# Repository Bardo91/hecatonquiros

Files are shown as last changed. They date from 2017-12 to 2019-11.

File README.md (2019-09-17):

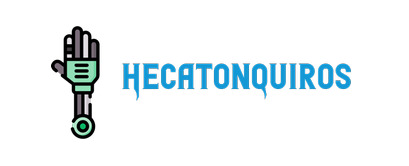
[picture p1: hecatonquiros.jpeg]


    

[WIKI](https://github.com/ViGUS/hecatonquiros/wiki)

Official doc in https://vigus.github.io/hecatonquiros/

# INSTALLATION

1. Install dependencies
```
git clone https://github.com/Bardo91/hecatonquiros
cd hecatonquiros
bash scripts/install_dependencies.sh
```
2. Compile library and install
```
cd build
cmake ..
make -j4
sudo make install
```

# TUTORIALS
[tutorial gazebo](https://github.com/ViGUS/hecatonquiros/wiki/Tutorial-gazebo)

# Arm models
###  PWM servos Model 4 DoF

###  Feetech serial servos Model 4 DoF
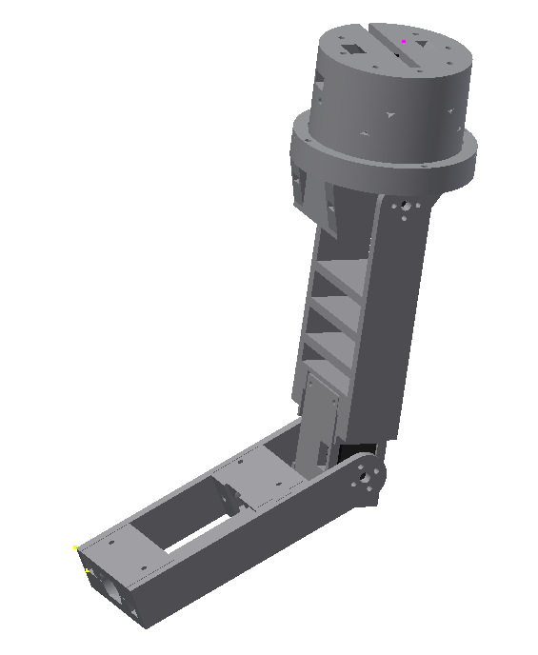
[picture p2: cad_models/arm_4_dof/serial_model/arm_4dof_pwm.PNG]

# Tools
### Gripper 0 Dof PWM
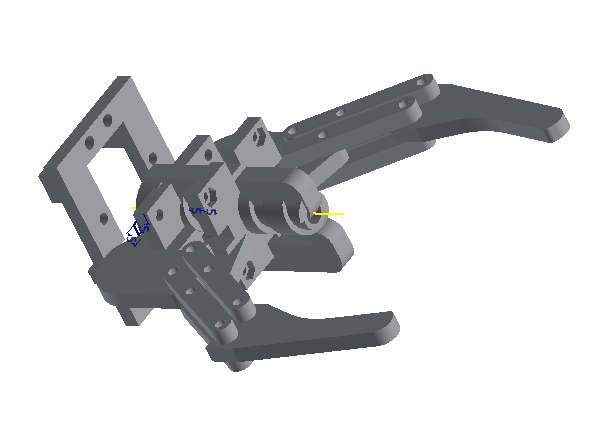
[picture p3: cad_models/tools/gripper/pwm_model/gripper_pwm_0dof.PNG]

### Gripper 1 Dof PWM
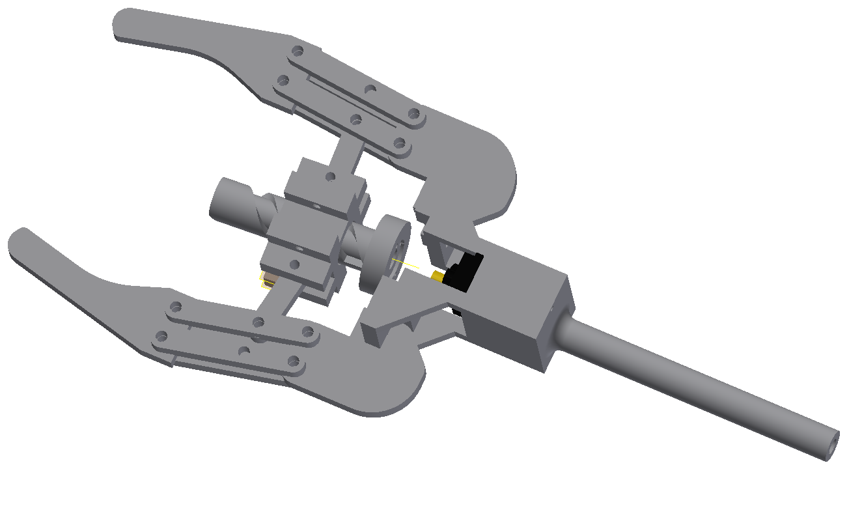
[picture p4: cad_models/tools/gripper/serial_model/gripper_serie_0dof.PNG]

### Gripper 2 Dof PWM
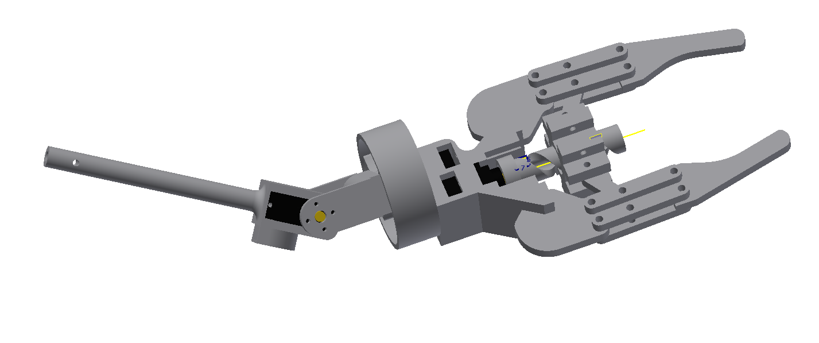
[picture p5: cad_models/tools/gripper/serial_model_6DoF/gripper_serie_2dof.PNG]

### Docking Tool
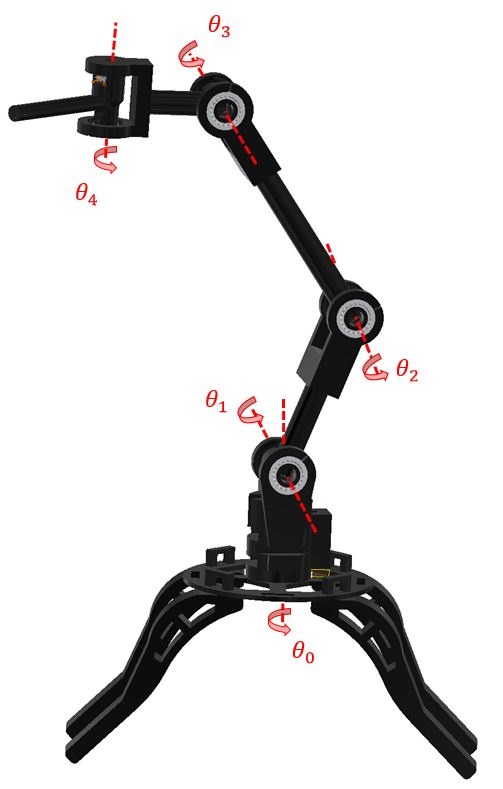
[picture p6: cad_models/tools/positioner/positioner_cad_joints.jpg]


# Arm Tester GUI
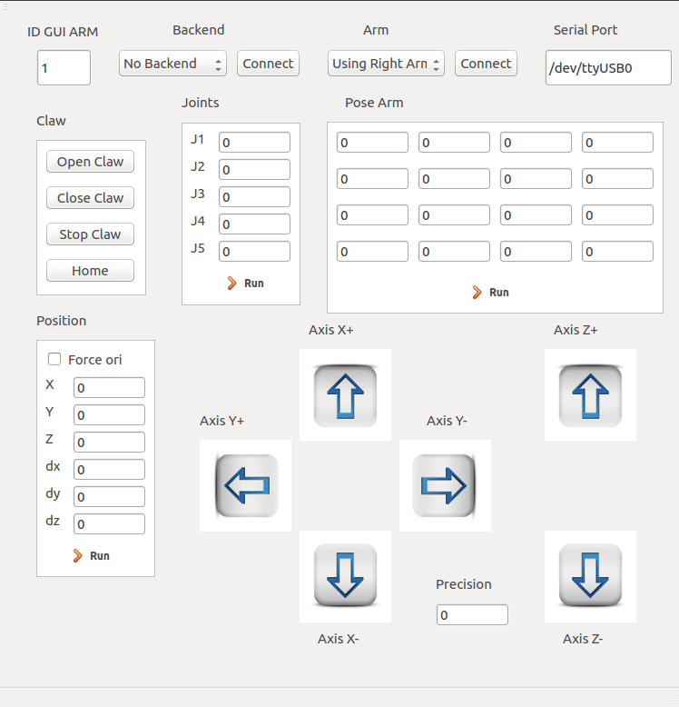
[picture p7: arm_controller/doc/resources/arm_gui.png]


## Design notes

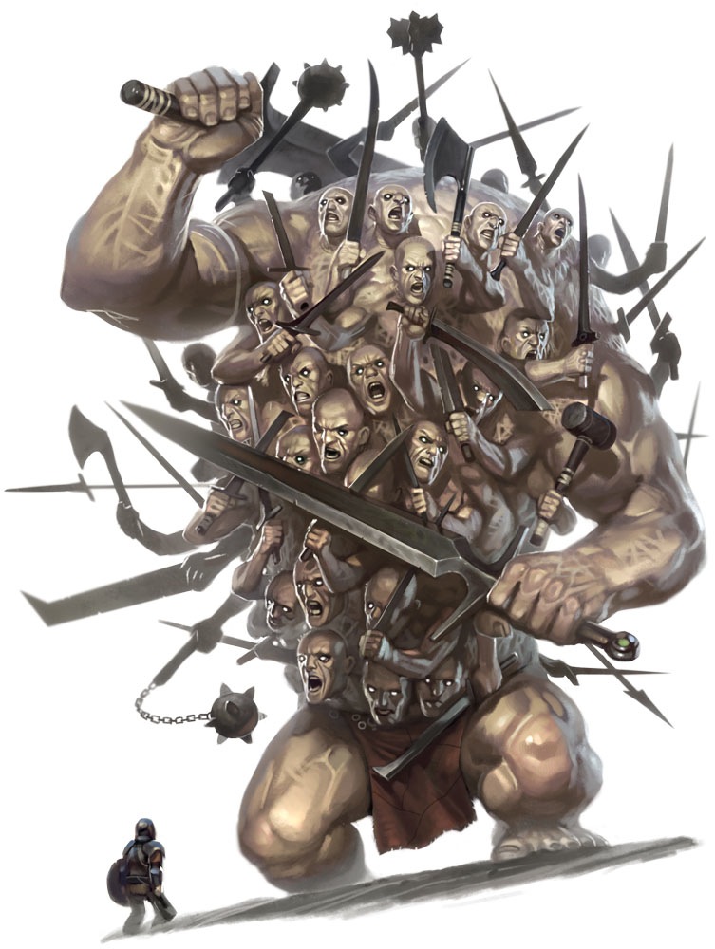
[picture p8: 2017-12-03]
arm_controller/doc/resources/hecatonquiros.jpg

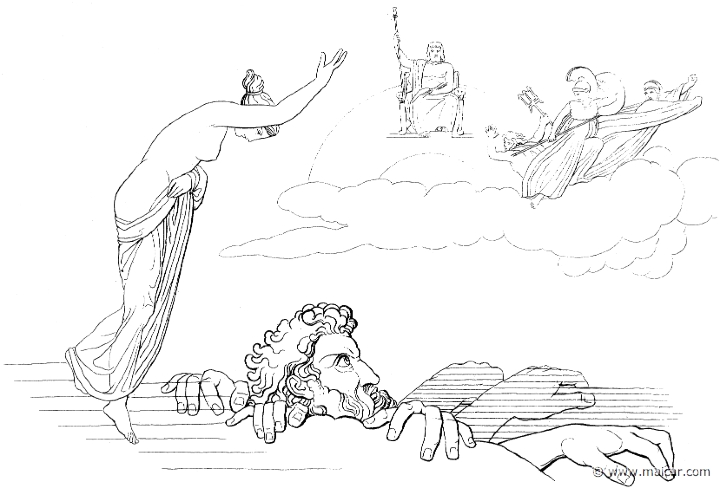
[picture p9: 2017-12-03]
arm_controller/doc/resources/hecatonquiros_2.jpg

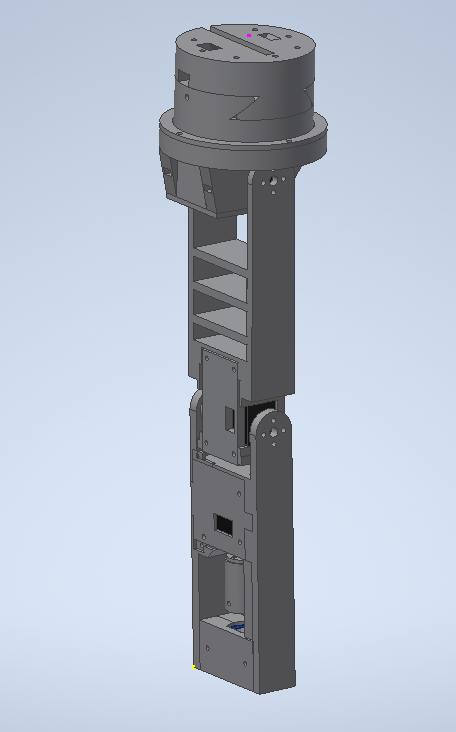
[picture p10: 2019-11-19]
cad_models/arm_4_dof/serial_model/arm_4dof_serial.PNG

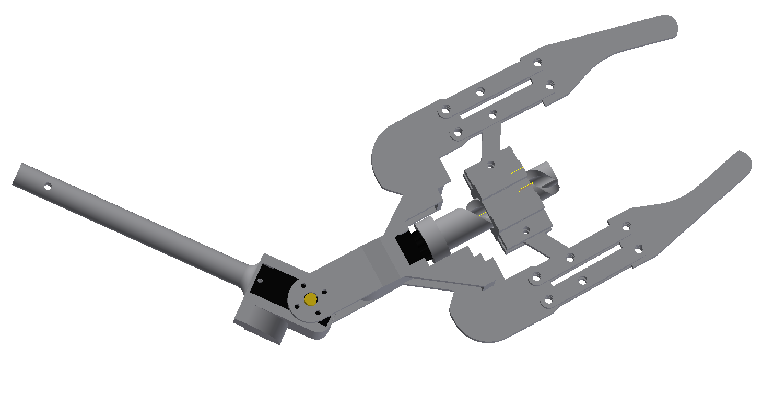
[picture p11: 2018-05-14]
cad_models/tools/gripper/serial_model_5DoF/gripper_serie_1dof.PNG

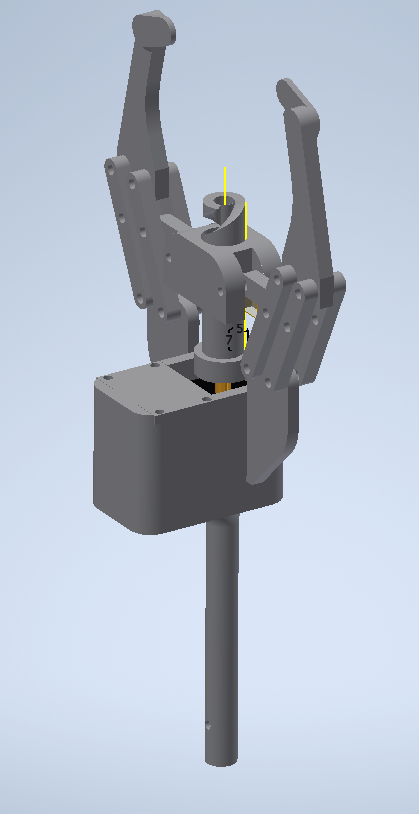
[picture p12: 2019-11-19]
cad_models/tools/gripper/serial_model_0dof/Gripper_0dof.PNG

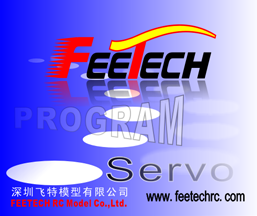
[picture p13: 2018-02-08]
tools/feetech_servo_library/FD Software-Open Source Code VS2008(170307)/FD-OPEN/bmp/PT.bmp

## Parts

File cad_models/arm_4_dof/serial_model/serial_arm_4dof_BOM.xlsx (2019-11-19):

Item | Part Number | Thumbnail | BOM Structure | QTY | Stock Number | Description | REV
1 | arm_0_attachment |  | Normal | 1
2 | arm_0_top |  | Normal | 1
3 | servo_FT_SC |  | Normal | 4
4 | arm_0_bottom |  | Normal | 1
5 | arm_0_bottom_top_lock |  | Normal | 1
6 | servo_FT_SC_horn_1 |  | Normal | 4
7 | arm_0_bottom_case |  | Normal | 1
8 | arm_1_v2 |  | Normal | 1
9 | servo_FT_SC_horn |  | Normal | 2
10 | arm_1_case |  | Normal | 1
11 | bearing |  | Normal | 2
12 | arm_2_case |  | Normal | 1
13 | arm_2_case_bearing |  | Normal | 1
14 | arm_2 |  | Normal | 1
15 | end_effector_connector_arm2_grande |  | Normal | 1

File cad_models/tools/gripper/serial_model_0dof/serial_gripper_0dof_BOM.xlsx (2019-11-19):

Item | Part Number | Thumbnail | BOM Structure | QTY | Stock Number | Description | REV
1 | core_attachment |  | Normal | 1
2 | case_core |  | Normal | 1
3 | bar |  | Normal | 8
4 | gripper |  | Normal | 2
5 | ScrewActuatorGripper |  | Normal | 1
6 | ScrewActuatorGripperCenter |  | Normal | 1
7 | barMini |  | Normal | 2
8 | feetech_sc215 |  | Normal | 1

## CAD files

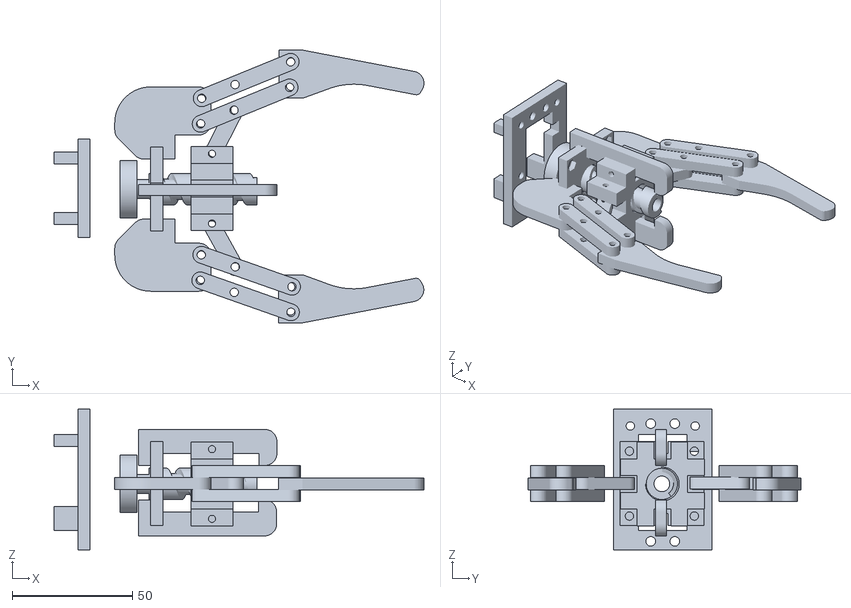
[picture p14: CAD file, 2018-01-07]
cad_models/tools/gripper/pwm_model/stl/gripper_complete.stl
153.9 x 113.5 x 58.5

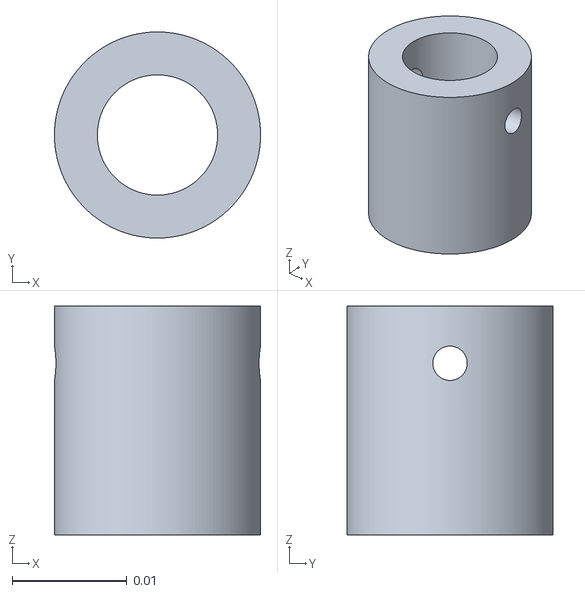
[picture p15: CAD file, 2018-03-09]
arm_controller/model/arm4dof/end_effector_connector.stl
0.018 x 0.018 x 0.02

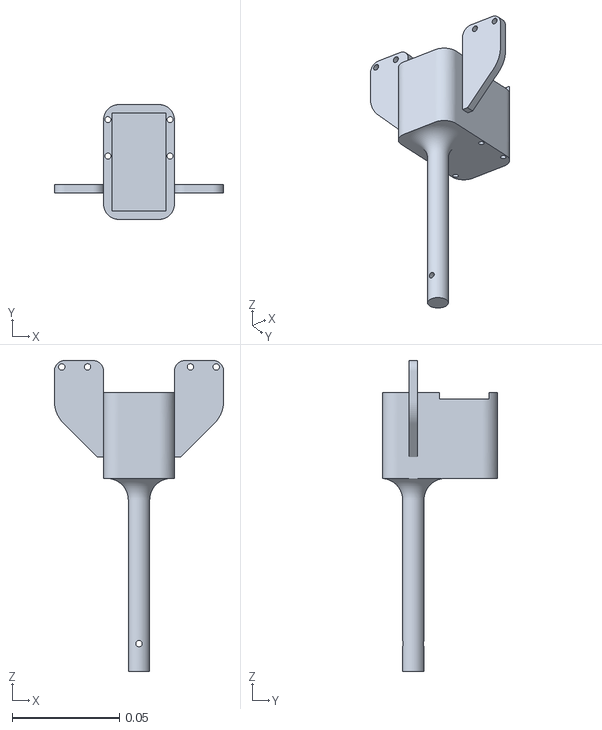
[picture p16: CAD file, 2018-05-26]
arm_controller/model/gripper0dof_strong/core_attachment.stl
0.079 x 0.0535 x 0.145

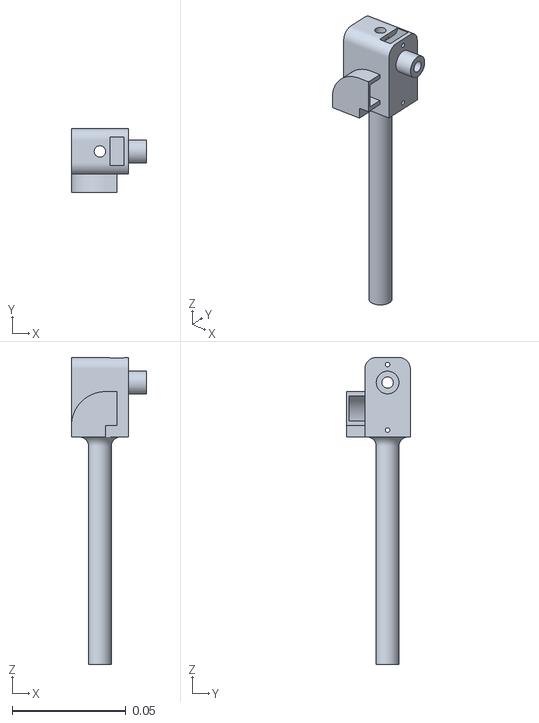
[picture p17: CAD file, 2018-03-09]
arm_controller/model/gripper2dof/core_structure.stl
0.033 x 0.028 x 0.135

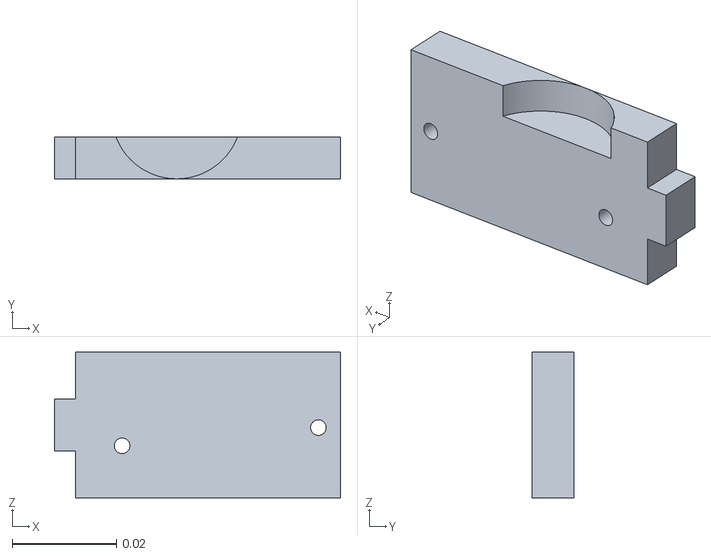
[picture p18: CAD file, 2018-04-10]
arm_description/meshes/new_meshes/arm_2_microservo_case.stl
0.055 x 0.008 x 0.028

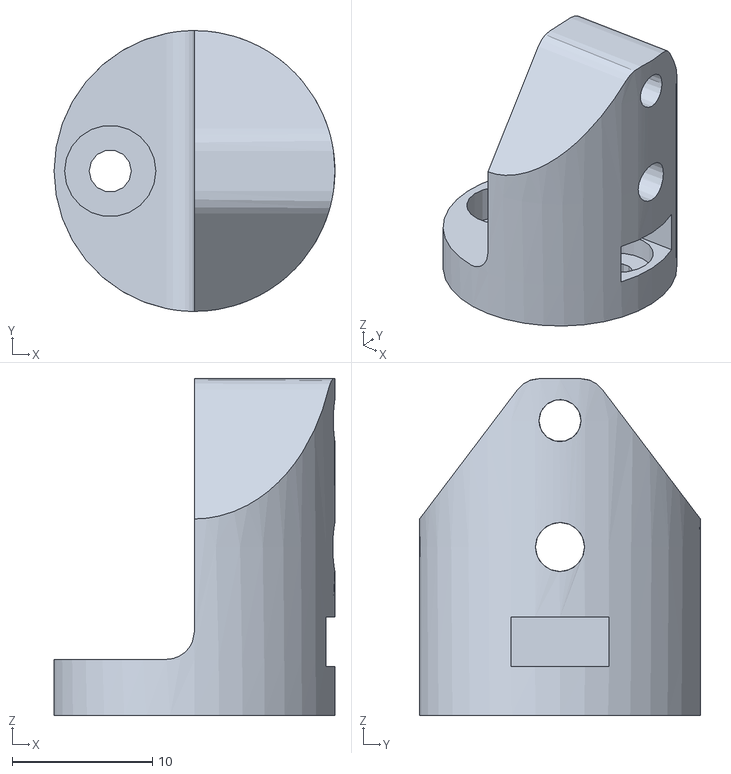
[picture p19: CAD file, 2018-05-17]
cad_models/accesories/camarasupport_robot.stl
20.0 x 20.0 x 24.0

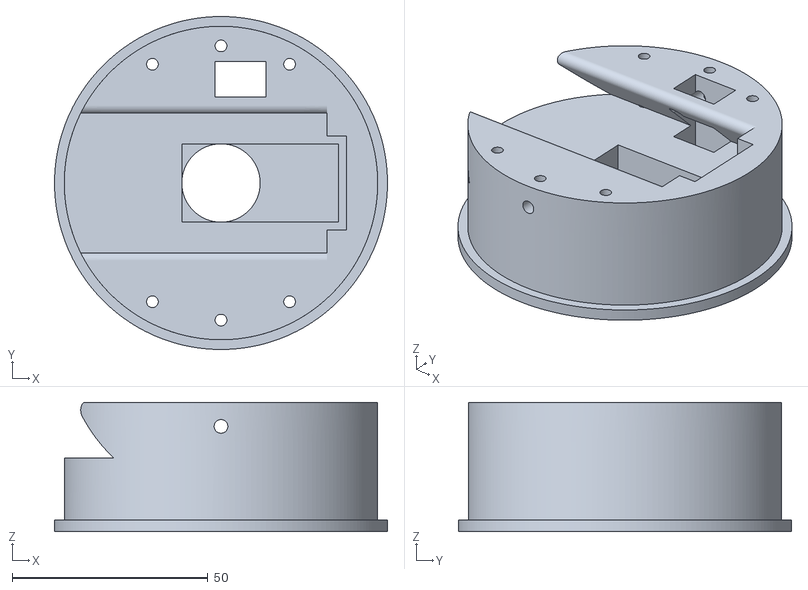
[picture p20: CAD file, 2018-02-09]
cad_models/arm_3_dog/serial_model/stl/arm_0_top.stl
85.0 x 85.0 x 33.0

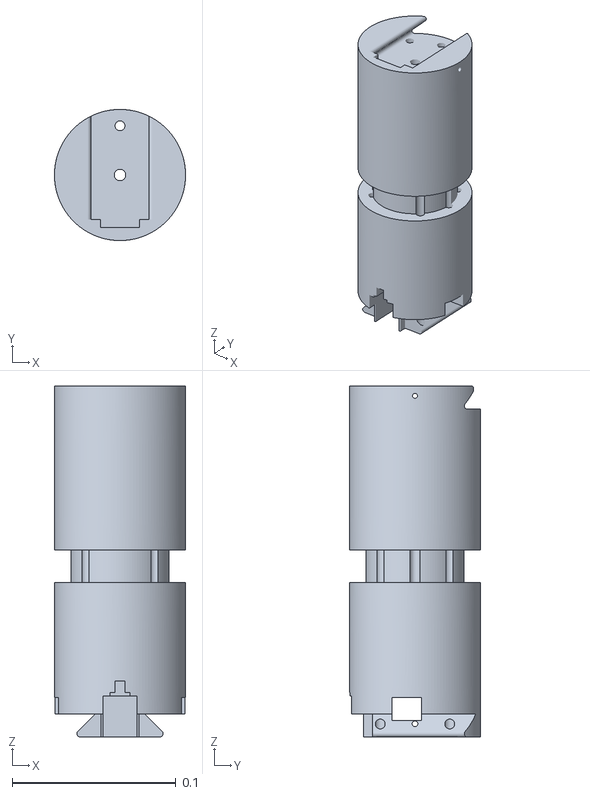
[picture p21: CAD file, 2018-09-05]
cad_models/arm_4_dof/serial_model/stl/arm_0_extension.stl
0.08 x 0.08 x 0.214

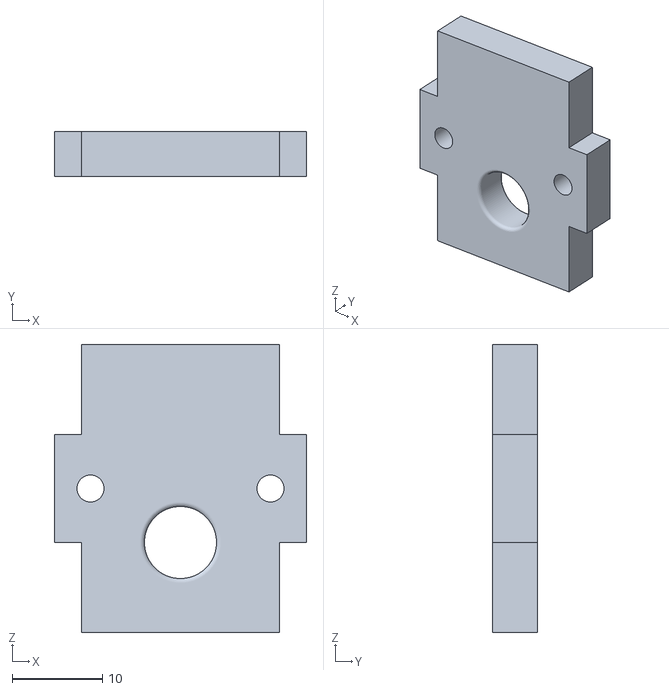
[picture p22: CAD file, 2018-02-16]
cad_models/tools/gripper/serial_model/stl/core_case.stl
28.0 x 5.00 x 32.0

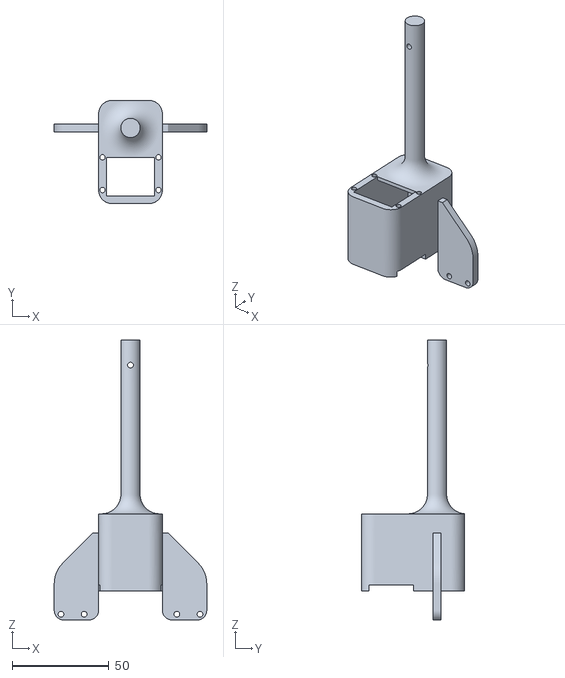
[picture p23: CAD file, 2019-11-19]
cad_models/tools/gripper/serial_model_0dof/stl/core_attachment.stl
79.0 x 53.5 x 145.0

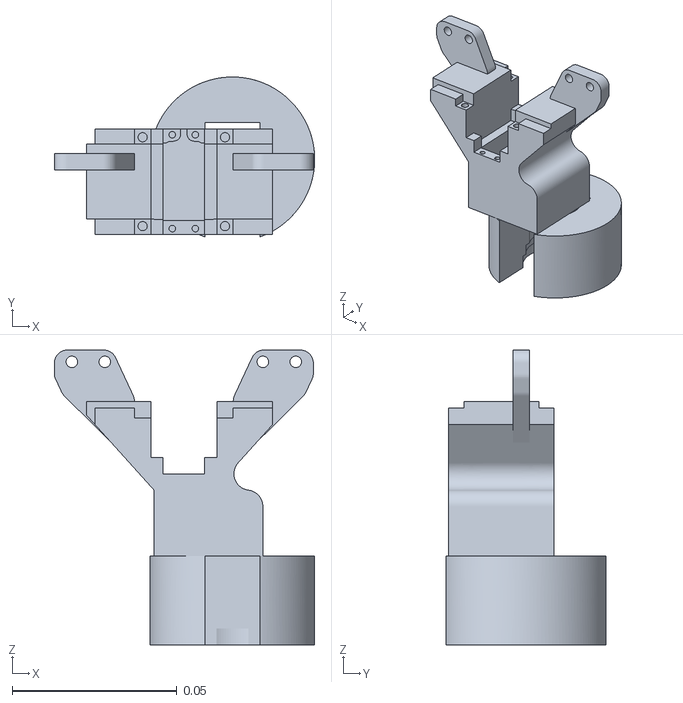
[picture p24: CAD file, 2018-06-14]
cad_models/tools/gripper/serial_model_bearing_6DoF/stl/base_gripper_v2.stl
0.0791 x 0.0486 x 0.0896

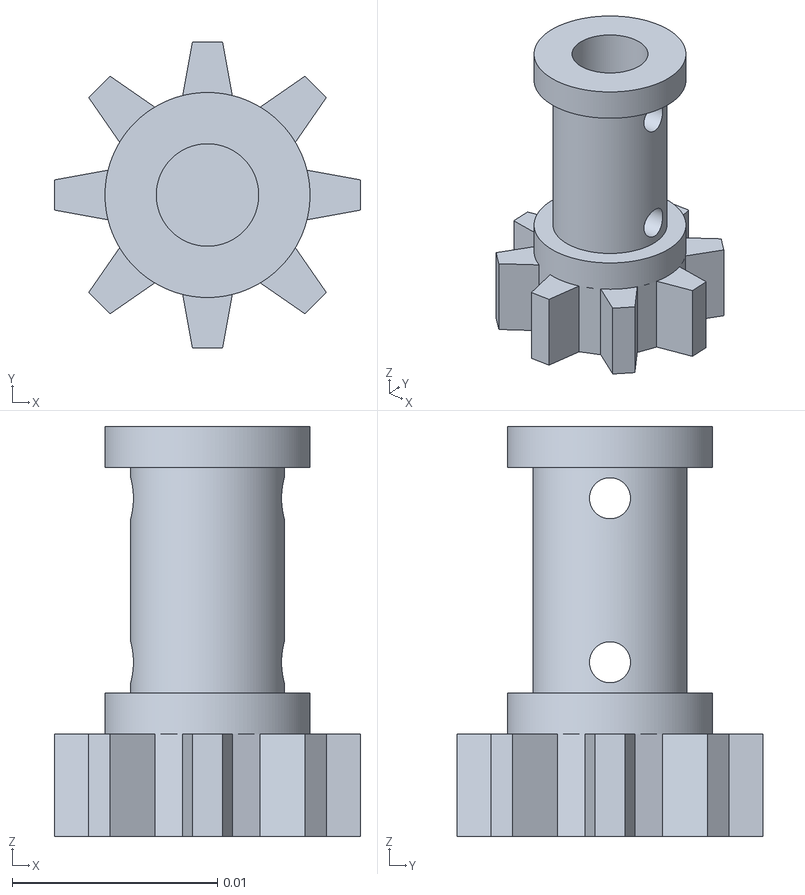
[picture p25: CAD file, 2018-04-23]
cad_models/tools/gripper/two_fingers_tensor/stl/eng_chic_2_1.stl
0.0149 x 0.0149 x 0.02

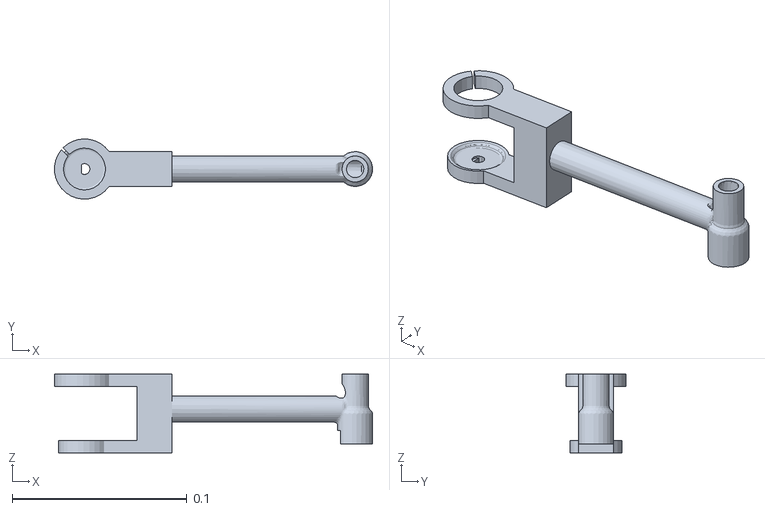
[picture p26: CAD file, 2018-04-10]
cad_models/tools/positioner/stl/Positioner_1.stl
0.182 x 0.0345 x 0.045

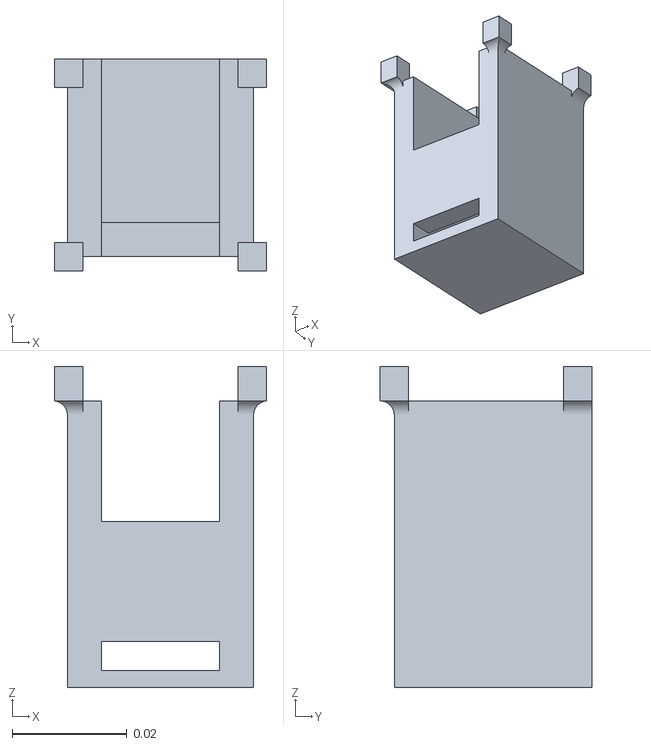
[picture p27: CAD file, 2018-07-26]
cad_models/tools/soft_gripper/stl/soft_gripper_base_1.stl
0.037 x 0.037 x 0.056

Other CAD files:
cad_models/tools/gripper/serial_model_5DoF/stl/core_structure.stl
tools/meshes/arm/bar2.stl
tools/meshes/positioner/bar2.stl
tools/meshes/uav/uav.stl
arm_controller/model/arm4dof/arm_0_attachment.stl
arm_controller/model/arm4dof/arm_0_bottom.stl
arm_controller/model/arm4dof/arm_0_bottom_case.stl
arm_controller/model/arm4dof/arm_0_bottom_top_lock.stl
arm_controller/model/arm4dof/arm_1.stl
arm_controller/model/arm4dof/arm_1_case.stl
arm_controller/model/arm4dof/arm_2_case.stl
arm_controller/model/arm4dof/arm_2_case_bearing.stl
arm_controller/model/arm4dof/arm_2_microservo.stl
arm_controller/model/arm4dof/arm_2_microservo_case.stl
arm_controller/model/gripper0dof_strong/ScrewActuatorGripperCenter.stl
arm_controller/model/gripper0dof_strong/case_core.stl
arm_controller/model/gripper0dof_strong/gripper.stl
arm_controller/model/gripper3dof/attachment.stl
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

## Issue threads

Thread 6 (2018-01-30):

Automatic calibration system for gripper offsets

Bardo91, 2018-01-30:

Bardo91, 2018-03-21:
@manuoso Using Feetech Backend and read joints with motors disabled and store values.

Bardo91, 2018-04-24:
Put the tool inside of hecatonquiros/tools/feetech_calibration

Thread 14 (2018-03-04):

Ejecution de trayectorias!

Bardo91, 2018-03-04:
Si se mandan de golpe muchas posiciones por ejemplo para una trajectoria, no hay garantia de que se ejecuten todos los pasos y no hay feedback de la posicion desde el arduino. Estudiar posibles soluciones

Bardo91, 2018-03-19:
Target this when  https://github.com/ViGUS/hecatonquiros/issues/26 is finished

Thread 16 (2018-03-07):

mapeo correcto de micro servos

Bardo91, 2018-03-07:

Closed 2018-03-08.

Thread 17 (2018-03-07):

Desarrollar mejor metodo de mapeo y offsets de joints

Bardo91, 2018-03-07:

Bardo91, 2018-03-07:
Repeated issue https://github.com/ViGUS/hecatonquiros/issues/6

Closed 2018-03-07.

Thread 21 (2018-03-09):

Weird different behaviour between Cpp and Python interfaces using same robot

Bardo91, 2018-03-09:
This is what I get using python
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

And this is what I obtain with cpp:
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

Bardo91, 2018-03-16:
Letting hecatonquiros transforms between quaternion and the rotation matrix solves the problem.

Closed 2018-03-16.

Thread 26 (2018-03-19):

Feetech driver from c++ code

Bardo91, 2018-03-19:
Avoid usage of Arduino for controlling FEETECH SCServos

Bardo91, 2018-03-19:
Implemented basic functionality in e67ffe373e16651e2d498f5aa2fd98a4979cd7ed, need intensive test with real arms

Closed 2018-04-02.

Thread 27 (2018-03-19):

Torque control with FEETECH SCServos

Bardo91, 2018-03-19:
When https://github.com/ViGUS/hecatonquiros/issues/26 is finished, add safety torque control

Bardo91, 2018-03-20:
Added watchdog in 04907ed41dcd0705e452b1e750118094cd18c16a but just couting a message. Tested with single servo, need to test with arms.

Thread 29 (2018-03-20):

Gripper actuator not working in all the interfaces

Bardo91, 2018-03-20:

Closed 2018-09-05.

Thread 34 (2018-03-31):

In Feetech back-end, add possibility of offsetting joints

Bardo91, 2018-03-31:

Bardo91, 2018-04-05:
Have you fixed this? @manuoso

manuoso, 2018-04-05:
We have now a tool for finer tune (MinMaxValues in map angle) but not implemented offset to these finer tune

Bardo91, 2018-04-05:
Well, I consider that this  tool is what we wanted. What I meant is if the code allows to use these values to each arm separately, or otherwise it is still hardcoded in the Arm4DoF class.

manuoso, 2018-04-05:
Ahh, Its still hardcoded in the Arm3DoF class, you receive these values and then you must put them in the class

Bardo91, 2018-04-05:
Ok, thanks

manuoso, 2018-04-24:
added option for use a xml for configure offsets

Closed 2018-04-24.

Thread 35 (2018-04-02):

ARM_2 (for big servo) the dummy axis of the servo does not fit into the model.

Bardo91, 2018-04-02:

Bardo91, 2018-04-05:
Did you fix this too?

manuoso, 2018-04-05:
Not yet...

Closed 2018-04-09.

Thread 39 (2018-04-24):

Put arm tester in hecatonquiros/tools

Bardo91, 2018-04-24:

manuoso, 2018-04-24:
and calibration feetech too

manuoso, 2019-03-26:
Done with manipulator controller tester and calibration feetech in tools

Closed 2019-03-26.

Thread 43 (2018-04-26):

Arm GUI

Bardo91, 2018-04-26:
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

manuoso, 2018-04-30:
add too a function to:
- Read position servo (be careful with the time...)
- Activate / Disable torque control

manuoso, 2019-03-26:
Arm GUI is designed, need to include in Tools

Closed 2019-03-26.

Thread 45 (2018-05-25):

Add method for disabling all servos or individual servos

Bardo91, 2018-05-25:

Bardo91, 2018-09-08:
Similar to https://github.com/ViGUS/hecatonquiros/issues/51

Closed 2018-09-04.

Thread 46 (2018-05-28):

Analyze problem with ACK of feetech servo

Bardo91, 2018-05-28:
Commented in commit 43ea90fa9c497bbc698820fc6389d8e891aa5cd4 due too large delays during the execution of the application

Bardo91, 2018-08-16:
I think it is related with the multithreading

Bardo91, 2018-09-08:
@manuoso  I think I re-enabled the the ACK after setting up the mutex system in the servo interface. So it should be done. Please, check it and close this issue

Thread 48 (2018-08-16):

Multithreaded joint read does not work

Bardo91, 2018-08-16:

Bardo91, 2018-08-16:
Esto deberia haber estado integrado con toda la interfaz de los brazos. Solo estaba hasta el punto de leer el valor del servo desde el backend, pero eso no tiene sentido cara hacia afuera, al brazo solo le interesan los angulos de los servos segun el mapeado y esto no existe en el codigo. Los joints leidos desde los brazos eran los virtuales.

Bardo91, 2018-08-16:
@manuoso Que prueba hiciste exactamente para probar lo de la lectura? Para saber que no me estoy volviendo loco

Bardo91, 2018-08-23:
@manuoso He medio arreglado esto. Pero necesitaria una inspeccion mas intensiva. Lo cierro por ahora por que funciona.

Closed 2018-08-23.

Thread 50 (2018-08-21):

Arm extension test and tune

Bardo91, 2018-08-21:
A new piece has been added to the folder of serial_arms, it is an extension of arms' attachment which lower the arms to make them operate farer from the propellers. But need to be printed and tested

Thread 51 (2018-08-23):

Added a proper way to disable servo torques for safety

Bardo91, 2018-08-23:

Bardo91, 2018-09-08:
Is it closed because you achieved it or because it is not possible? I remember you told me that it was not working yet

Closed 2018-09-04.

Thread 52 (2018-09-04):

Some errors in reading position of each servo

manuoso, 2018-09-04:
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

Are these errors due to requesting the position at high speed, from the servo itself or due to something else?

Bardo91, 2018-09-08:
@manuoso  Do you have any clue about this?

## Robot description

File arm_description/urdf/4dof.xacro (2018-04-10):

<?xml version="1.0" encoding="UTF-8"?>
<robot name="aeroarms" xmlns:xacro="http://www.ros.org/wiki/xacro">
   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
  <xacro:property name="PI" value="3.1415926535897931"/>
  <xacro:property name="mass" value="0.5" /> 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
  <xacro:property name="width" value="0.1" /> 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
  <xacro:property name="height1" value="2" /> 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
  <xacro:property name="height2" value="1" /> 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
  <xacro:property name="height3" value="1" /> 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
  <xacro:property name="camera_link" value="0.05" /> 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
  <xacro:property name="axel_offset" value="0.05" /> 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


   <link name="base_link">
      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
   </link>
   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
    <link name="left/arm_0_attachment">
      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

          <inertial>
      <origin rpy="0 0 0" xyz="0 0 0" />
      <mass value="${mass}"/>
      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
    </inertial>

   </link>
   <joint name="left/arm_0_attachment_joint" type="fixed">
      <parent link="base_link" />
      <child link="left/arm_0_attachment" />
      <origin rpy="0 0 0" xyz="0 0.1 -0.1" />
   </joint>

<link name="left/arm_0_top">
       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

    <inertial>
      <origin rpy="0 0 0" xyz="0 0 0" />
      <mass value="${mass}"/>
      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
    </inertial>

    </link>
    <joint name="left/arm_0_top_joint" type="fixed">
       <parent link="left/arm_0_attachment" />
       <child link="left/arm_0_top" />
       <origin rpy="0 0 0" xyz="0 0 -0.03" />
    </joint>

    <link name="left/arm_0_bottom_top_lock">
       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

    <inertial>
      <origin rpy="0 0 0" xyz="0 0 0" />
      <mass value="${mass}"/>
      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
    </inertial>

    </link>
    <joint name="left/arm_0_bottom_top_lock_joint" type="fixed">
       <parent link="left/arm_0_top" />
       <child link="left/arm_0_bottom_top_lock" />
       <origin rpy="0 0 0" xyz="0 0 0" />
    </joint>


   <link name="left/arm_0_bottom">
      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

    <inertial>
      <origin rpy="0 0 0" xyz="0 0 0" />
      <mass value="${mass}"/>
      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
    </inertial>

   </link>
   <joint name="left/arm_0_bottom_joint" type="continuous">
      <parent link="left/arm_0_bottom_top_lock" />
      <child link="left/arm_0_bottom" />
      <origin rpy="0 ${-pi/2} ${-pi/2}" xyz="0 0 -0.005" />
   </joint>

    <link name="left/arm_0_bottom_case">
      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

    <inertial>
      <origin rpy="0 0 0" xyz="0 0 0" />
      <mass value="${mass}"/>
      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
    </inertial>

   </link>
   <joint name="left/arm_0_bottom_case_joint" type="fixed">
      <parent link="left/arm_0_bottom" />
      <child link="left/arm_0_bottom_case" />
      <origin rpy="0 0 0" xyz="-0.017 0 0" />
   </joint>

   
   <link name="left/arm_1">
      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

    <inertial>
      <origin rpy="0 0 0" xyz="0 0 0" />
      <mass value="${mass}"/>
      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
    </inertial>

   </link>
   <joint name="left/arm_1_joint" type="continuous">
      <parent link="left/arm_0_bottom_case" />
      <child link="left/arm_1" />
      <origin xyz="0 0 0" rpy="0 ${3*pi/2} 0" />
   </joint>


 <link name="left/arm_1_case">
      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

    <inertial>
      <origin rpy="0 0 0" xyz="0 0 0" />
      <mass value="${mass}"/>
      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
    </inertial>

   </link>
   <joint name="left/arm_1_case_joint" type="fixed">
      <parent link="left/arm_1" />
      <child link="left/arm_1_case" />
      <origin xyz="0 0 0.145" rpy="0 0 0" />
   </joint>
   
   
   <link name="left/arm_2_microservo">
      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

    <inertial>
      <origin rpy="0 0 0" xyz="0 0 0" />
      <mass value="${mass}"/>
      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
    </inertial>

   </link>
   <joint name="left/arm_2_microservo_joint" type="continuous">
      <parent link="left/arm_1_case" />
      <child link="left/arm_2_microservo" />
      <origin xyz="0 0 0.0085" rpy="0 0 0"/>
   </joint>

<link name="left/arm_2_microservo_case">
      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


          <inertial>
      <origin rpy="0 0 0" xyz="0 0 0" />
      <mass value="${mass}"/>
      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
    </inertial>
   </link>
   <joint name="left/arm_2_microservo_case_joint" type="fixed">
      <parent link="left/arm_2_microservo" />
      <child link="left/arm_2_microservo_case" />
      <origin xyz="0 0 0.057" rpy="0 0 0"/>
   </joint>

<link name="left/arm_2_case_bearing">
      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

    <inertial>
      <origin rpy="0 0 0" xyz="0 0 0" />
      <mass value="${mass}"/>
      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
    </inertial>

   </link>
   <joint name="left/arm_2_case_bearing_joint" type="fixed">
      <parent link="left/arm_2_microservo_case" />
      <child link="left/arm_2_case_bearing" />
      <origin xyz="0 0 0.072" rpy="0 0 0"/>
   </joint>

<link name="left/end_effector_connector">
      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

    <inertial>
      <origin rpy="0 0 0" xyz="0 0 0" />
      <mass value="${mass}"/>
      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
    </inertial>

   </link>
   <joint name="left/end_effector_connector_joint" type="fixed">
      <parent link="left/arm_2_case_bearing" />
      <child link="left/end_effector_connector" />
      <origin xyz="0 0 0" rpy="0 0 0"/>
   </joint>



<link name="left/core_structure">
      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

    <inertial>
      <origin rpy="0 0 0" xyz="0 0 0" />
      <mass value="${mass}"/>
      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
    </inertial>

   </link>
   <joint name="left/core_structure_joint" type="fixed">
      <parent link="left/end_effector_connector" />
      <child link="left/core_structure" />
      <origin xyz="0 0 0" rpy="0 0 0"/>
   </joint>

   <link name="left/base_gripper">
      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

    <inertial>
      <origin rpy="0 0 0" xyz="0 0 0" />
      <mass value="${mass}"/>
      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
    </inertial>

   </link>
   <joint name="left/base_gripper_joint" type="continuous">
      <parent link="left/core_structure" />
      <child link="left/base_gripper" />
      <origin xyz="0 0 0.041" rpy="0 0 ${-pi/2}"/>
   </joint>


<link name="left/microservo_FT">
      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

    <inertial>
      <origin rpy="0 0 0" xyz="0 0 0" />
      <mass value="${mass}"/>
      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
    </inertial>

   </link>
   <joint name="left/microservo_FT_joint" type="fixed">
      <parent link="left/base_gripper" />
      <child link="left/microservo_FT" />
      <origin xyz="0 0 0.057" rpy="${pi/2} 0 ${pi/2}"/>
   </joint>

<link name="left/ScrewActuatorGripper">
      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

    <inertial>
      <origin rpy="0 0 0" xyz="0 0 0" />
      <mass value="${mass}"/>
      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
    </inertial>

   </link>
   <joint name="left/ScrewActuatorGripper_joint" type="fixed">
      <parent link="left/microservo_FT" />
      <child link="left/ScrewActuatorGripper" />
      <origin xyz="0 0 0" rpy="${-pi/2} 0 0"/>
   </joint>

<link name="left/base_gripper_case">
      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

    <inertial>
      <origin rpy="0 0 0" xyz="0 0 0" />
      <mass value="${mass}"/>
      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
    </inertial>

   </link>
   <joint name="left/base_gripper_case_joint" type="fixed">
      <parent link="left/ScrewActuatorGripper" />
      <child link="left/base_gripper_case" />
      <origin xyz="0 0 0" rpy="0 0 0"/>
   </joint>

   <link name="left/ScrewActuatorGripperCenter">
      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

    <inertial>
      <origin rpy="0 0 0" xyz="0 0 0" />
      <mass value="${mass}"/>
      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
    </inertial>

   </link>
   <joint name="left/ScrewActuatorGripperCenter_joint" type="fixed">
      <parent link="left/ScrewActuatorGripper" />
      <child link="left/ScrewActuatorGripperCenter" />
      <origin xyz="0 0 0" rpy="0 0 0"/>
   </joint>



<link name="left/holdBar_left">
      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

    <inertial>
      <origin rpy="0 0 0" xyz="0 0 0" />
      <mass value="${mass}"/>
      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
    </inertial>

   </link>
   <joint name="left/holdBar_left_joint" type="fixed">
      <parent link="left/base_gripper" />
      <child link="left/holdBar_left" />
      <origin xyz="0 -0.02 0.057" rpy="0 0 0"/>
   </joint>

   <link name="left/holdBar_right">
      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

    <inertial>
      <origin rpy="0 0 0" xyz="0 0 0" />
      <mass value="${mass}"/>
      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
    </inertial>

   </link>
   <joint name="left/holdBar_right_joint" type="fixed">
      <parent link="left/base_gripper" />
      <child link="left/holdBar_right" />
      <origin xyz="0 0.02 0.057" rpy="0 0 0"/>
   </joint>


   <link name="left/left_bar1">
      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

    <inertial>
      <origin rpy="0 0 0" xyz="0 0 0" />
      <mass value="${mass}"/>
      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
    </inertial>
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

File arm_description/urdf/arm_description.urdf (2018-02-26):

<?xml version="1.0" encoding="UTF-8"?>
<robot name="arm4DoF">
   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
   <link name="base_link">
      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
   </link>

   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
    <link name="left/arm_0_top">
      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
   </link>
   <joint name="left/arm_0_top_joint" type="fixed">
      <parent link="base_link" />
      <child link="left/arm_0_top" />
      <origin rpy="0 0 0" xyz="0 1 0" />
   </joint>


    <link name="left/arm_0_closing_case">
       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
    </link>
    <joint name="left/arm_0_closing_case_joint" type="fixed">
       <parent link="left/arm_0_top" />
       <child link="left/arm_0_closing_case" />
       <origin rpy="0 0 0" xyz="0 0 -0.07" />
    </joint>

   <link name="left/arm_0_bottom">
      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
   </link>
   <joint name="left/arm_0_bottom_joint" type="continuous">
      <parent link="left/arm_0_closing_case" />
      <child link="left/arm_0_bottom" />
      <origin rpy="0 ${pi/2} 0" xyz="0 0 -0.335" />
   </joint>

   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
   <link name="left/arm_1">
      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
   </link>
   <joint name="left/arm_1_joint" type="continuous">
      <parent link="left/arm_0_bottom" />
      <child link="left/arm_1" />
      <origin xyz="0 0 0" rpy="${pi/2} 0 ${pi/2}" />
   </joint>

   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
   <link name="left/arm_2">
      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
   </link>
   <joint name="left/arm_2_joint" type="continuous">
      <parent link="left/arm_1" />
      <child link="left/arm_2" />
      <origin xyz="0 0 1.7" rpy="0 0 0"/>
   </joint>


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
    <link name="right/arm_0_top">
      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
    </link>
    <joint name="right/arm_0_top_joint" type="fixed">
       <parent link="base_link" />
       <child link="right/arm_0_top" />
       <origin rpy="0 0 0" xyz="0 -1 0" />
    </joint>

    <link name="right/arm_0_closing_case">
       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
    </link>
    <joint name="right/arm_0_closing_case_joint" type="fixed">
       <parent link="right/arm_0_top" />
       <child link="right/arm_0_closing_case" />
       <origin rpy="0 0 0" xyz="0 0 -0.07" />
    </joint>

    <link name="right/arm_0_bottom">
      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
    </link>
    <joint name="right/arm_0_bottom_joint" type="continuous">
      <parent link="right/arm_0_closing_case" />
      <child link="right/arm_0_bottom" />
      <origin rpy="0 ${pi/2} 0" xyz="0 0 -0.335" />
    </joint>

    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
    <link name="right/arm_1">
      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
    </link>
    <joint name="right/arm_1_joint" type="continuous">
      <parent link="right/arm_0_bottom" />
      <child link="right/arm_1" />
      <origin xyz="0 0 0" rpy="${pi/2} 0 ${pi/2}" />
    </joint>

    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
    <link name="right/arm_2">
      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
    </link>
    <joint name="right/arm_2_joint" type="continuous">
      <parent link="right/arm_1" />
      <child link="right/arm_2" />
      <origin xyz="0 0 1.7" rpy="0 0 0"/>
    </joint>




</robot>

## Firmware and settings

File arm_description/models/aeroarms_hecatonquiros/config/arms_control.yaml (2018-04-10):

aeroarms:

  # Joint State Controller
  joint_state_controller:
    type: joint_state_controller/JointStateController
    publish_rate: 20

  # Position Controllers
  # Left arm
  q1_1_position_controller:
    type: effort_controllers/JointPositionController
    joint: q1_1
    pid: {p: 1.0, i: 0.5, d: 0.0, i_clamp: 2.0}

  q1_2_position_controller:
    type: effort_controllers/JointPositionController
    joint: q1_2
    pid: {p: 1.0, i: 0.5, d: 0.0, i_clamp: 2.0}

  q1_3_position_controller:
    type: effort_controllers/JointPositionController
    joint: q1_3
    pid: {p: 1.0, i: 0.5, d: 0.0, i_clamp: 2.0}

  q1_4_position_controller:
    type: effort_controllers/JointPositionController
    joint: q1_4
    pid: {p: 0.25, i: 0.1, d: 0.0, i_clamp: 1.0}

  # Right arm
  q2_1_position_controller:
    type: effort_controllers/JointPositionController
    joint: q2_1
    pid: {p: 1.0, i: 0.5, d: 0.0, i_clamp: 2.0}

  q2_2_position_controller:
    type: effort_controllers/JointPositionController
    joint: q2_2
    pid: {p: 1.0, i: 0.5, d: 0.0, i_clamp: 2.0}

  q2_3_position_controller:
    type: effort_controllers/JointPositionController
    joint: q2_3
    pid: {p: 1.0, i: 0.5, d: 0.0, i_clamp: 2.0}

  q2_4_position_controller:
    type: effort_controllers/JointPositionController
    joint: q2_4
    pid: {p: 0.25, i: 0.1, d: 0.0, i_clamp: 1.0}


  #Hecatonquiros arm
  left/arm_0_bottom_joint_position_controller:
    type: effort_controllers/JointPositionController
    joint: left/arm_0_bottom_joint
    pid: {p: 100.0, i: 0.01, d: 10.0}
  left/arm_1_joint_position_controller:
    type: effort_controllers/JointPositionController
    joint: left/arm_1_joint
    pid: {p: 100.0, i: 0.01, d: 10.0}
  left/arm_2_microservo_joint_position_controller:
    type: effort_controllers/JointPositionController
    joint: left/arm_2_microservo_joint
    pid: {p: 100.0, i: 0.01, d: 10.0}
  left/base_gripper_joint_position_controller:
    type: effort_controllers/JointPositionController
    joint: left/base_gripper_joint
    pid: {p: 100.0, i: 0.01, d: 10.0}
  left/left_gripper_joint_position_controller:
    type: effort_controllers/JointPositionController
    joint: left/left_gripper_joint
    pid: {p: 100.0, i: 0.01, d: 10.0}
  left/right_gripper_joint_position_controller:
    type: effort_controllers/JointPositionController
    joint: left/right_gripper_joint
    pid: {p: 100.0, i: 0.01, d: 10.0}

  #Right arm
  right/arm_0_bottom_joint_position_controller:
    type: effort_controllers/JointPositionController
    joint: right/arm_0_bottom_joint
    pid: {p: 100.0, i: 0.01, d: 10.0}
  right/arm_1_joint_position_controller:
    type: effort_controllers/JointPositionController
    joint: right/arm_1_joint
    pid: {p: 100.0, i: 0.01, d: 10.0}
  right/arm_2_microservo_joint_position_controller:
    type: effort_controllers/JointPositionController
    joint: right/arm_2_microservo_joint
    pid: {p: 100.0, i: 0.01, d: 10.0}
  right/base_gripper_joint_position_controller:
    type: effort_controllers/JointPositionController
    joint: right/base_gripper_joint
    pid: {p: 100.0, i: 0.01, d: 10.0}
  right/left_gripper_joint_position_controller:
    type: effort_controllers/JointPositionController
    joint: right/left_gripper_joint
    pid: {p: 100.0, i: 0.01, d: 10.0}
  right/right_gripper_joint_position_controller:
    type: effort_controllers/JointPositionController
    joint: right/right_gripper_joint
    pid: {p: 100.0, i: 0.01, d: 10.0}

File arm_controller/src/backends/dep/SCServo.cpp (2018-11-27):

// FEETECH DRIVER
//
//	Original code from FEETECH company. 2016.8.9
//
//
//	Adapted version for C++. 2018-04-19
//


#include <hecatonquiros/backends/dep/SCServo.h>

SCServo::SCServo(std::string _serialPort) {
	Level = 1;
	End = 1;
	if(mSerial == nullptr){
		if(this->init(_serialPort)){
			mSerial = mSerialPorts[_serialPort];
		}
	}
	
}

//---------------------------------------------------------------------------------------------------------------------
bool SCServo::isConnected(){
	try {
		return mSerial != nullptr && mSerial->isOpen();
	}catch (std::exception& e){
		std::cerr << e.what() << std::endl;
	}
	return false;
}

//---------------------------------------------------------------------------------------------------------------------
int SCServo::EnableTorque(u8 ID, u8 Enable) {
	return writeByte(ID, P_TORQUE_ENABLE, Enable);
}

//---------------------------------------------------------------------------------------------------------------------
int SCServo::WritePos(u8 ID, u16 Position, u16 Time, u16 Speed) {
	return writePos(ID, Position, Time, Speed, INST_WRITE);
}

//---------------------------------------------------------------------------------------------------------------------
int SCServo::RegWritePos(u8 ID, u16 Position, u16 Time, u16 Speed) {
	return writePos(ID, Position, Time, Speed, INST_REG_WRITE);
}

//---------------------------------------------------------------------------------------------------------------------
void SCServo::SyncWritePos(u8 ID[], u8 IDN, u16 Position[], u16 Time[], u16 Speed[]) {
	try {
		mSerial->flush();		
		u8 *buf_send[IDN];					
		u8 buf[6];
		for (int i = 0; i<IDN; i++){
			Host2SCS(buf+0, buf+1, Position[i]);
			Host2SCS(buf+2, buf+3, Time[i]);
			Host2SCS(buf+4, buf+5, Speed[i]);
			buf_send[i] = new u8 [6];						// 666 TODO FREE MEMORY
			std::memcpy(buf_send[i], buf, sizeof(u8)*6);
		}
		syncWrite(ID, IDN, P_GOAL_POSITION_L, buf_send, 6);	
	}catch (std::exception& e){
		std::cerr << e.what() << std::endl;
	}
}

//---------------------------------------------------------------------------------------------------------------------
int SCServo::ReadPos(u8 ID) {
	return readWord(ID, P_PRESENT_POSITION_L);
}

//---------------------------------------------------------------------------------------------------------------------
//---------------------------------------------------------------------------------------------------------------------
//---------------------------------------------------------------------------------------------------------------------
//---------------------------------------------------------------------------------------------------------------------
//---------------------------------------------------------------------------------------------------------------------
//---------------------------------------------------------------------------------------------------------------------
void SCServo::Host2SCS(u8 *DataL, u8* DataH, int Data) {
	if(End) {
		*DataL = (Data>>8);
		*DataH = (Data&0xff);
	} else {
		*DataH = (Data>>8);
		*DataL = (Data&0xff);
	}
}

//---------------------------------------------------------------------------------------------------------------------
int SCServo::SCS2Host(u8 DataL, u8 DataH) {
	int Data;
	if(End){
		Data = DataL;
		Data<<=8;
		Data |= DataH;
	}else{
		Data = DataH;
		Data<<=8;
		Data |= DataL;
	}
	return Data;
}

//---------------------------------------------------------------------------------------------------------------------
void SCServo::writeBuf(u8 ID, u8 MemAddr, u8 *nDat, u8 nLen, u8 Fun) {

	try {
		u8 msgLen = 2;
		u8 bBuf[6];
		u8 CheckSum = 0;
		bBuf[0] = 0xff;
		bBuf[1] = 0xff;
		bBuf[2] = ID;
		bBuf[4] = Fun;
		if(nDat){
			msgLen += nLen + 1;
			bBuf[3] = msgLen;
			bBuf[5] = MemAddr;
			mSerial->write(bBuf, 6);		
		}else{
			bBuf[3] = msgLen;
			mSerial->write(bBuf, 5);		
		}
		CheckSum = ID + msgLen + Fun + MemAddr;
		u8 i = 0;
		if(nDat){
			for(i=0; i<nLen; i++){
				CheckSum += nDat[i];
			}
		}
		mSerial->write(nDat, nLen);
		u8 negCheckSum = ~CheckSum;
		mSerial->write(&negCheckSum, 1);	
	}catch (std::exception& e){
		std::cerr << e.what() << std::endl;
	}		
}

//---------------------------------------------------------------------------------------------------------------------
int SCServo::genWrite(u8 ID, u8 MemAddr, u8 *nDat, u8 nLen) {
	try {
		mSerial->flush();		
	}catch (std::exception& e){
		std::cerr << e.what() << std::endl;
	}
	writeBuf(ID, MemAddr, nDat, nLen, INST_WRITE);
	return Ack(ID);
}

//---------------------------------------------------------------------------------------------------------------------
int SCServo::regWrite(u8 ID, u8 MemAddr, u8 *nDat, u8 nLen) {
	try {
		mSerial->flush();		
	}catch (std::exception& e){
		std::cerr << e.what() << std::endl;
	}
	writeBuf(ID, MemAddr, nDat, nLen, INST_REG_WRITE);
	return Ack(ID);
}

//---------------------------------------------------------------------------------------------------------------------
void SCServo::syncWrite(u8 ID[], u8 IDN, u8 MemAddr, u8 *nDat[], u8 nLen) {
	try {
		u8 mesLen = ((nLen+1)*IDN+4);
		u8 Sum = 0;
		u8 bBuf[7];
		bBuf[0] = 0xff;
		bBuf[1] = 0xff;
		bBuf[2] = 0xfe;
		bBuf[3] = mesLen;
		bBuf[4] = INST_SYNC_WRITE;
		bBuf[5] = MemAddr;
		bBuf[6] = nLen;
		mSerial->write(bBuf, 7);

		Sum = 0xfe + mesLen + INST_SYNC_WRITE + MemAddr + nLen;
		u8 i, j, k;
		for(i=0; i<IDN; i++){
			mSerial->write(&ID[i],1);
			mSerial->write(nDat[i], nLen);
			//std::cout << "nDat: " << (int) *nDat[i] << std::endl;

			Sum += ID[i];
			for(j=0; j<nLen; j++){
					Sum += nDat[i][j];
			}
		}
		u8 negSum = ~Sum;
		mSerial->write(&negSum,1);		
	}catch (std::exception& e){
		std::cerr << e.what() << std::endl;
	}
}

//---------------------------------------------------------------------------------------------------------------------
int SCServo::writeByte(u8 ID, u8 MemAddr, u8 bDat) {
	try {
		mSerial->flush();		
	}catch (std::exception& e){
		std::cerr << e.what() << std::endl;
	}
	writeBuf(ID, MemAddr, &bDat, 1, INST_WRITE);
	return Ack(ID);
}

//---------------------------------------------------------------------------------------------------------------------
int SCServo::writeWord(u8 ID, u8 MemAddr, u16 wDat) {
	try {
		mSerial->flush();		
	}catch (std::exception& e){
		std::cerr << e.what() << std::endl;
	}
	u8 buf[2];
	Host2SCS(buf+0, buf+1, wDat);
	writeBuf(ID, MemAddr, buf, 2, INST_WRITE);
	return Ack(ID);
}


//---------------------------------------------------------------------------------------------------------------------
int SCServo::writePos(u8 ID, u16 Position, u16 Time, u16 Speed, u8 Fun) {
	try {
		mSerial->flush();		
	}catch (std::exception& e){
		std::cerr << e.what() << std::endl;
	}
	u8 buf[6];
	Host2SCS(buf+0, buf+1, Position);
	Host2SCS(buf+2, buf+3, Time);
	Host2SCS(buf+4, buf+5, Speed);
	writeBuf(ID, P_GOAL_POSITION_L, buf, 6, Fun);
	return Ack(ID);
	//return 1;
}
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

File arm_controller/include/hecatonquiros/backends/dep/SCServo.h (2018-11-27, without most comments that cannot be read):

// FEETECH DRIVER
//
//	Original code from FEETECH company. 2016.8.9
//
//
//	Adapted version for C++. 2018-04-19
//

#ifndef HECATONQUIROS_ARMCONTROLLER_BACKENDS_DEP_SCSERVO_h_
#define HECATONQUIROS_ARMCONTROLLER_BACKENDS_DEP_SCSERVO_h_

#include <string>
#include <mutex>
#include <map>
#include <iostream>
#include <stdio.h>

#include <serial/serial.h>

/// \brief Class for controlling SC servos from FEETECH.
/// The class takes control of the given serial port and it is thread safe
class SCServo{
	private: // Static methods
		static std::map<std::string, serial::Serial*> mSerialPorts;

		// Initialize or get serial port if exists
		static bool init(std::string &_portName){
			if(mSerialPorts.find(_portName) != mSerialPorts.end()){
				return true;
			}else{
				try {
					serial::Serial *serial = new serial::Serial(_portName, 1000000, serial::Timeout::simpleTimeout(30));
					if(serial->isOpen()){
						mSerialPorts[_portName] = serial;
						return true;
					}else{
						return false;
					}
				}catch (std::exception& e){
					std::cerr << e.what() << std::endl;
				}
			}
		}

	public:	// Custom types
		typedef		char			s8;
		typedef		unsigned char	u8;	
		typedef		unsigned short	u16;	
		typedef		short			s16;
		typedef		unsigned long	u32;	
		typedef		long			s32;

	public:
		/// Default constructor. Initializes internal variables and serial port
		/// \brief _port: given serial port
		SCServo(std::string _serialPort);
		bool isConnected();
		void SyncWritePos(u8 ID[], u8 IDN, u16 Position[], u16 Time[], u16 Speed[] = 0);
		int ReadPos(u8 ID);
		int WritePos(u8 ID, u16 Position, u16 Time, u16 Speed = 0);
		int ReadLoadH(u8 ID);
		int EnableTorque(u8 ID, u8 Enable);



	private:

		int genWrite(u8 ID, u8 MemAddr, u8 *nDat, u8 nLen);
		int regWrite(u8 ID, u8 MemAddr,u8 *nDat, u8 nLen);
		void syncWrite(u8 ID[], u8 IDN, u8 MemAddr, u8 *nDat[], u8 nLen);
		int writeByte(u8 ID, u8 MemAddr, u8 bDat);
		int writeWord(u8 ID, u8 MemAddr, u16 wDat);
		int RegWritePos(u8 ID, u16 Position, u16 Time, u16 Speed = 0);
		void RegWriteAction();
		int WriteSpe(u8 ID, s16 Speed);
		int Read(u8 ID, u8 MemAddr, u8 *nData, u8 nLen);
		int readByte(u8 ID, u8 MemAddr);
		int readWord(u8 ID, u8 MemAddr);
		int ReadVoltage(u8 ID);
		int ReadTemper(u8 ID);
		int ReadLoadL(u8 ID);
		int Ping(u8 ID);
		void reBoot(u8 ID);
		int wheelMode(u8 ID);
		int joinMode(u8 ID, u16 minAngle=0, u16 maxAngle=1023);
		int Reset(u8 ID);
	public:
		u8	Level;
		u8	End;

	private:
		serial::Serial *mSerial = nullptr;
		std::mutex mLocker;
		
	private:
		void writeBuf(u8 ID, u8 MemAddr, u8 *nDat, u8 nLen, u8 Fun);
		int writePos(u8 ID, u16 Position, u16 Time, u16 Speed, u8 Fun);
		void Host2SCS(u8 *DataL, u8* DataH, int Data);
		int	SCS2Host(u8 DataL, u8 DataH);
		int	Ack(u8 ID);

		#define		B_1M		0
		#define		B_0_5M		1
		#define		B_250K		2
		#define		B_128K		3
		#define		B_115200	4
		#define		B_76800		5
		#define		B_57600		6
		#define		B_38400		7

		//register Address
		#define P_MODEL_NUMBER_L 0
		#define P_MODEL_NUMBER_H 1
		#define P_VERSION_L 3		
		#define P_VERSION_H 4
		#define P_ID 5
		#define P_BAUD_RATE 6
		#define P_RETURN_DELAY_TIME 7
		#define P_RETURN_LEVEL 8
		#define P_MIN_ANGLE_LIMIT_L 9
		#define P_MIN_ANGLE_LIMIT_H 10
		#define P_MAX_ANGLE_LIMIT_L 11
		#define P_MAX_ANGLE_LIMIT_H 12
		#define P_LIMIT_TEMPERATURE 13
		#define P_MAX_LIMIT_VOLTAGE 14
		#define P_MIN_LIMIT_VOLTAGE 15
		#define P_MAX_TORQUE_L 16
		#define P_MAX_TORQUE_H 17
		#define P_ALARM_LED 18
		#define P_ALARM_SHUTDOWN 19
		#define P_COMPLIANCE_P 21
		#define P_COMPLIANCE_D 22
		#define P_COMPLIANCE_I 23
		#define P_PUNCH_L 24
		#define P_PUNCH_H 25
		#define P_CW_DEAD 26
		#define P_CCW_DEAD 27
		#define P_IMAX_L 28
		#define P_IMAX_H 29

		#define P_TORQUE_ENABLE 40
		#define P_LED 41
		#define P_GOAL_POSITION_L 42
		#define P_GOAL_POSITION_H 43
		#define P_GOAL_TIME_L 44
		#define P_GOAL_TIME_H 45
		#define P_GOAL_SPEED_L 46
		#define P_GOAL_SPEED_H 47
		#define P_LOCK 48

		#define P_PRESENT_POSITION_L 56
		#define P_PRESENT_POSITION_H 57
		#define P_PRESENT_SPEED_L 58
		#define P_PRESENT_SPEED_H 59
		#define P_PRESENT_LOAD_L 60
		#define P_PRESENT_LOAD_H 61
		#define P_PRESENT_VOLTAGE 62
		#define P_PRESENT_TEMPERATURE 63
		#define P_REGISTERED_INSTRUCTION 64
		#define P_ERROR 65
		#define P_MOVING 66
		#define P_VIR_POSITION_L 67
		#define P_VIR_POSITION_H 68

		//Instruction:
		#define INST_PING 0x01
		#define INST_READ 0x02
		#define INST_WRITE 0x03
		#define INST_REG_WRITE 0x04
		#define INST_ACTION 0x05
		#define INST_RESET 0x06
		#define	INST_REBOOT	0x08
		#define INST_SYNC_WRITE 0x83
};
#endif

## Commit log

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2017-12-03 Added latest version of arm model.
    [arm_0_bottom.ipt, arm_0_bottom.stl, arm_0_closing_case.ipt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]
2017-12-03 Added latest version of cad model
    [Positioner_1.ipt, Positioner_1.stl, Positioner_2.ipt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]
2017-12-03 Added gripper latest model
    [Assembly.iam, Assembly2.iam, ScrewActuatorGripper.ipt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]
2017-12-03 Started design of new arm model using serial servos FT-SC
    [Assembly.iam, arm_0_attachment.ipt, arm_0_top.ipt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]
2017-12-03 WIP: arm_0 with serial servos
    [Assembly.iam, arm_0_bottom.ipt]
2017-12-04 Draft version of arm_0 parts
    [Assembly.iam, arm_0_bottom.ipt, arm_0_bottom_case.ipt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]
2017-12-04 Added horns models and other minor changes
    [Assembly.iam, arm_0_bottom.ipt, arm_0_bottom_case.ipt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]
2017-12-11 Update model serial servo with holes for wires
    [servo_FT_SC.ipt]
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2017-12-12 Fixed errors in measure of some parts
    [servo_FT_SC.ipt]
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2018-01-07 findind proper rotation of stl files
    [arm_0_bottom.stl, arm_1.stl, arm_2.stl]
2018-01-07 fixed visualization
    [arm_0_bottom.stl, arm_1.stl, arm_2.stl]
2018-01-07 added first model of complete gripper for display purposes
    [gripper_complete.stl]
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2018-01-28 Added gazebo simulation, changes for compila project with backends, WIP: backend gazebo
    [arm_0_bottom.stl, arm_0_closing_case.stl, arm_0_top.stl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]
2018-01-28 fixes namespaces
    [arm_description.urdf]
2018-01-29 Fixed backendArduino and joints of Arm4DoF
    [Arm4DoF.h]
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2018-02-05 New models serial servos, not finished
    [arm_1.ipt, arm_2.ipt, arm_2_case_bearing.ipt]
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2018-02-06 New version for serial servo in arm 1
    [arm_1.ipt, arm_1_case.ipt]
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2018-02-08 New models for arm 2, include microservo serial and normal servo serial
    [arm_2.ipt, arm_2_case.ipt, arm_2_microservo.ipt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]
2018-02-09 Fixed errors in new model
    [arm_2.ipt, arm_2_case.ipt]
2018-02-09 Fixed errors and added stl
    [arm_1.stl, arm_1_case.stl, arm_2.ipt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]
2018-02-09 Updated arm_0_bottom and created STLs
    [T_leg.stl, arm_0_bottom.ipt, arm_0_bottom.stl]
2018-02-09 Updated attachment and top pieces of arm_0 and compiled stls
    [Assembly.iam, arm_0_attachment.ipt, arm_0_attachment.stl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]
2018-02-09 Slightly modified servo and horn. Cable fixes in arm_0
    [Assembly.iam, arm_0_bottom.ipt, arm_0_bottom_case.ipt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]
2018-02-09 Added arm_1 to assembly
    [Assembly.iam]
2018-02-09 Fixed cable hole in arm_0 and updated assembly
    [Assembly.iam, arm_0_top.ipt]
2018-02-09 Last version of arm_0 with cable holes
    [Assembly.iam, arm_0_bottom.ipt, arm_0_bottom.stl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]
2018-02-09 guide for cable of second servo in arm_0_bottom
    [Assembly.iam, arm_0_bottom.ipt, arm_0_bottom.stl]
2018-02-09 Added engraved arrow for assembly guidelines
    [Assembly.iam, arm_0_bottom.ipt, arm_0_bottom.stl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]
2018-02-11 Several fixes after printing and first printable version of arm 1
    [Assembly.iam, arm_0_bottom.ipt, arm_0_bottom.stl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]
2018-02-11 fixes post printing
    [arm_0_attachment.ipt, arm_0_attachment.stl, arm_0_bottom_top_lock.stl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]
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2018-02-12 renamed gripper to gripper pwm to add also the gripper serial
    [Assembly.iam, Assembly2.iam, ScrewActuatorGripper.ipt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]
2018-02-13 First gripper and minor fixes in arm_2
    [Assembly.iam, Assembly1.iam, ScrewActuatorGripper.ipt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]
2018-02-13 added hole for unplugging the connector
    [arm_0_top.ipt]
2018-02-13 Fixed some errors
    [arm_2_case_bearing.stl, arm_2_microservo.ipt, arm_2_microservo.stl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]
2018-02-13 Added tunnel for arm 1
    [arm_1.ipt, arm_1.stl]
2018-02-13 Fixed errors in models and added stl for screw
    [ScrewActuatorGripper.ipt, ScrewActuatorGripper.stl, arm_0_bottom.ipt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]
2018-02-13 Both arms in rviz
    [arm_description.urdf, both_arms.urdf]
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2018-02-15 Added hole in arm_1_case
    [Assembly.iam, arm_1_case.ipt, arm_1_case.stl]
2018-02-15 Fixed some errors in arms and arduino firmware
    [arm_1.ipt, arm_1.stl, arm_1_case.ipt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]
2018-02-16 Fixed errors in arm 2
    [arm_2_case_bearing.ipt, arm_2_case_bearing.stl, arm_2_microservo.ipt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]
2018-02-16 Finish model for core gripper
    [core_case.ipt, core_case.stl, core_structure.stl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]
2018-02-18 Added model for gripper that adds the 5th DoF
    [Assembly.iam, ScrewActuatorGripper.ipt, ScrewActuatorGripperCenter.ipt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]
2018-02-18 Improved assembly of base_gripper
    [Assembly.iam, base_gripper.ipt, core_structure.ipt]
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2018-02-18 Added stl models of gripper_5dof
    [ScrewActuatorGripper.stl, ScrewActuatorGripperCenter.stl, bar.stl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]
2018-02-19 Fixed base gripper of gripper 5dof
    [base_gripper.ipt, base_gripper.stl, base_gripper_case.ipt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]
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2018-02-21 Both arms fixed.
    [arm_0_bottom.stl, arm_0_closing_case.stl, arm_0_top.stl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]
2018-02-21 Updated arm_2 serial with cable guides
    [arm_2_case_bearing.ipt, arm_2_case_bearing.stl, arm_2_microservo.ipt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]
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2018-02-24 Exported stls in meters instead of in millimeters
    [ScrewActuatorGripper.stl, ScrewActuatorGripperCenter.stl, arm_0_attachment.stl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]
2018-02-24 Initially fixed model
    [arm_1.stl, arm_2.stl, arm_2_microservo.stl]
2018-02-24 Added stl models, trying to attach gripper to arm
    [ScrewActuatorGripper.stl, ScrewActuatorGripperCenter.stl, arm_0_attachment.stl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]
2018-02-25 Working with translation3D need to check a few things and ignoring self-collisions but doing something.
    [arm_gripper_5dof.robot.xml]
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2018-02-28 Move arm to origin
    [arm_gripper_5dof.robot.xml]
2018-02-28 Fixed joint set when given joints are less than needed
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2018-02-28 Almost finished gripper kinbody
    [barMini.stl]
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2018-02-28 Removed gripper bodyparts due to problem generating IK model.
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2018-03-09 Changed model to use DH axis
    [arm_0_attachment.stl, arm_0_bottom.stl, arm_1.stl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]
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2018-03-11 WIP: 5dofIK currently model creation crashes
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2018-03-16 Fixed https://github.com/ViGUS/hecatonquiros/issues/15
    [arm_0_bottom.ipt, arm_0_bottom.stl]
2018-03-16 Fixed https://github.com/ViGUS/hecatonquiros/issues/11
    [core_structure.ipt, core_structure.stl]
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2018-03-21 Fixed first joint direction in arm_gripper_6dof. Commented load watchdog and min max angles for map values
    [BackendFeetech.cpp]
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2018-04-03 Updated gripper with fingers for a better visualization and collision check
    [bar.stl, base_gripper_case.stl, gripper.stl]
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2018-04-05 New version end effector and attachment for arm2 big
    [attachment_arm2_grande.ipt, attachment_arm2_grande.stl, end_effector_connector_arm2_grande.ipt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]
2018-04-05 Removed unused positioner parts and scaled to m instead of mm for simulations
    [Positioner_1.stl, Positioner_2.stl, Positioner_Adapter.ipt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]
2018-04-06 fixed errors in end effector
    [end_effector_connector_arm2_grande.ipt, end_effector_connector_arm2_grande.stl]
2018-04-06 Fixed others errors, faltaba un agujero
    [end_effector_connector_arm2_grande.ipt, end_effector_connector_arm2_grande.stl]
2018-04-09 Fixed pull request #35
    [arm_2.ipt, arm_2.stl, arm_2_case.ipt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]
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2018-04-12 some files of new version of gripper, working on it
    [finger_long.ipt, finger_short.ipt]
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2018-04-17 Fixed an error
    [finger_short.ipt, finger_short.stl]
2018-04-23 Fixed operations with claw
    [BackendFeetech.cpp]
2018-04-23 Eigen dependencia and fixed error servodriver
    [BackendFeetech.cpp]
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2018-04-25 Fixed arm rotation.
    [arm_gripper_6dof.robot.xml]
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2018-04-25 new version of attachment and middle joint with servos 2322
    [attachment_arm2_grande_microsevometalico.ipt, attachment_arm2_grande_microsevometalico.stl, middle_joint_microservo_metalico.ipt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]
2018-04-26 fixed some errors because of new version of function joints
    [main.cpp]
2018-04-26 fixed a needed hole
    [attachment_arm2_grande_microsevometalico.ipt, attachment_arm2_grande_microsevometalico.stl]
2018-04-27 fixed configs for new servo and other minor changes
    [BackendFeetech.cpp, main.cpp]
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2018-05-08 fixed error that convert a float number in int using QueryFloatText
    [BackendFeetech.cpp]
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2018-05-25 added new gripper 0dof with strong serial motor
    [ScrewActuatorGripper.stl, ScrewActuatorGripperCenter.stl, arm_gripper_6dof_4dof_strong.robot.xml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]
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2018-05-27 Fixed error of quaternions (order of elements) works better but not always converge
    [main.cpp]
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2018-06-04 updated cad models of gripper 6dof with bearings
    [Assembly_v2.iam, attachment_arm2_grande_microsevometalico.ipt, base_gripper_v2.ipt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]
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2018-08-10 minor fix
    [embrague_2_1.ipt]
2018-08-12 Fixes in models
    [Bevel Gear22.ipt, Bevel Gear22.stl, Bevel Gear22_opposite.ipt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]
2018-08-12 increased resolution of stls and scaled to mm
    [Bevel Gear22.stl, Bevel Gear22_opposite.stl, servoplace.stl]
2018-08-16 restored source folder moved wrongly
    [BackendFeetech.cpp]
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2018-08-16 supposedly reading real pose from servos but not working apparently
2018-08-16 fixed floating point values
    [BackendFeetech.cpp]
2018-08-16 Endedup using static mutex in feetech backend.
    When setting the mutex in SCServo something was not going, but if doing it outside works perfectly. Should be something intermedial that I am missing but will be marked for later
    [BackendFeetech.cpp, SCServo.cpp, SCServo.h]
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2018-08-17 Writing id to which comm failed
    [BackendFeetech.cpp]
2018-08-17 Fixed error in pipeline with claws
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2018-08-21 fixed rotation of 4dof arm
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2018-08-24 Keepingboth short and long version
    [Bevel Gear22.ipt, Bevel Gear22.stl, Bevel Gear22_long.ipt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]
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2018-08-27 fixed error of offset in read value from feetech
    [BackendFeetech.cpp]
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2018-09-04 added disable/enable torque but not works and other changes in individual arm controller
    [Arm4DoF.h, BackendFeetech.cpp]
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2018-09-12 added pose_line3d (problems in step size) and pose4d (need to check)
    [main.cpp]
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2018-09-20 fixed syncwrite for more than 6 servos
    [SCServo.cpp]
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2018-09-27 fix support gimbal
    [gimbal_soporte.CATPart, gimbal_soporte.stl]
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2018-09-27 fixed errors in plotter joints, now work fine
    [main.cpp]
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2018-10-10 frame fix
    [tablilla.CATPart, tablilla.stl]
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2018-10-24 fix hole undercarriage
    [rigido_trenaterrizaje.CATPart, rigido_trenaterrizaje.stl]
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2018-11-08 leica fix
    [pilar probeta.CATPart, pilar probeta.stl, soporte leica.CATPart]
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2019-07-22 Created model for simple4dof robot and testing in python to generate model
    [arm_4dof.robot.xml]
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2019-11-19 Updated 4dof arm and 0 dof gripper. Added BOMs and assembly videos
    [Assembly.iam, Assembly.ipn, Assembly1.iam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]
